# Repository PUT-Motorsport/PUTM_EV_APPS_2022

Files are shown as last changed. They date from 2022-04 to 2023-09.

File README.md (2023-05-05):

# Accelerator Pedal Position Sensor (APPS)

## Motivation

APPS handling is required by official FSG Rules according to T11.8 ([see](https://www.formulastudent.de/fileadmin/user_upload/all/2022/rules/FS-Rules_2022_v1.0.pdf#page=58)). APPS signals are system critical signals meaning that any implausibility between sensors or a failure should result in complete motor power shutdown.

## Pedal travel

* 0% - fully released
* 100% - fully applied

## Implausiblity

Implausibility is defined as a deviation of more than ten percentage points pedal travel
between any of the used APPSs. If it occurs for more than 100 ms the power to the motor must be immediately shut down.

## Platform

Software for APPS signal handling is developed using C++ for STM32 microcontroller.

## Program schematic

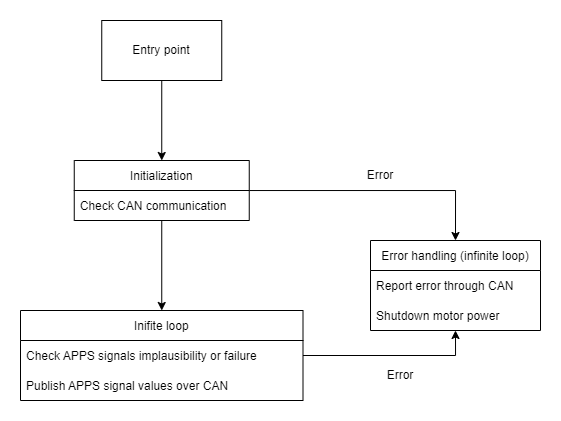
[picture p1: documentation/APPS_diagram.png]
APPS diagram


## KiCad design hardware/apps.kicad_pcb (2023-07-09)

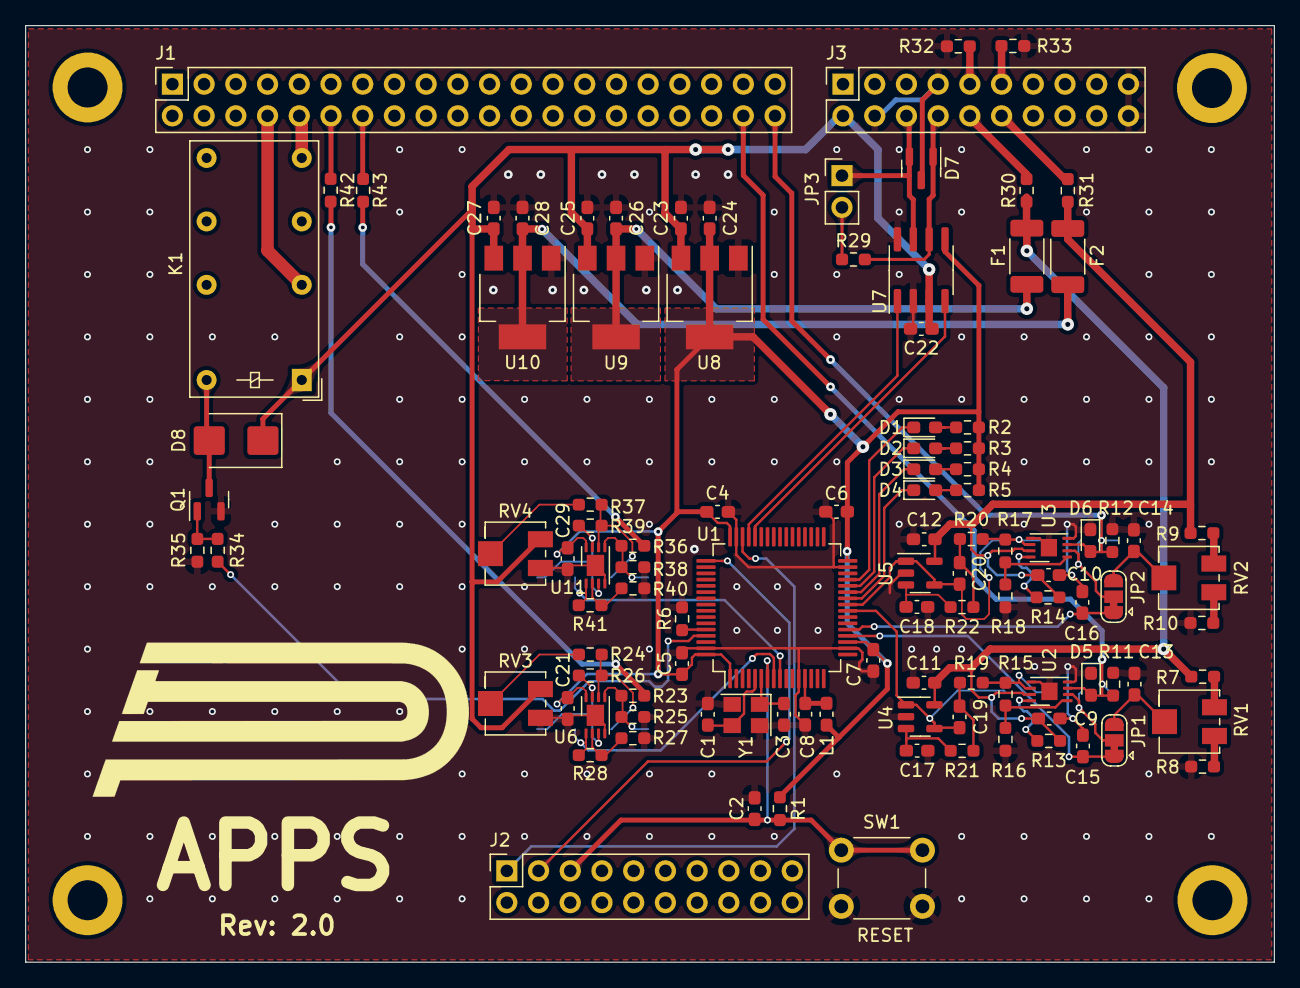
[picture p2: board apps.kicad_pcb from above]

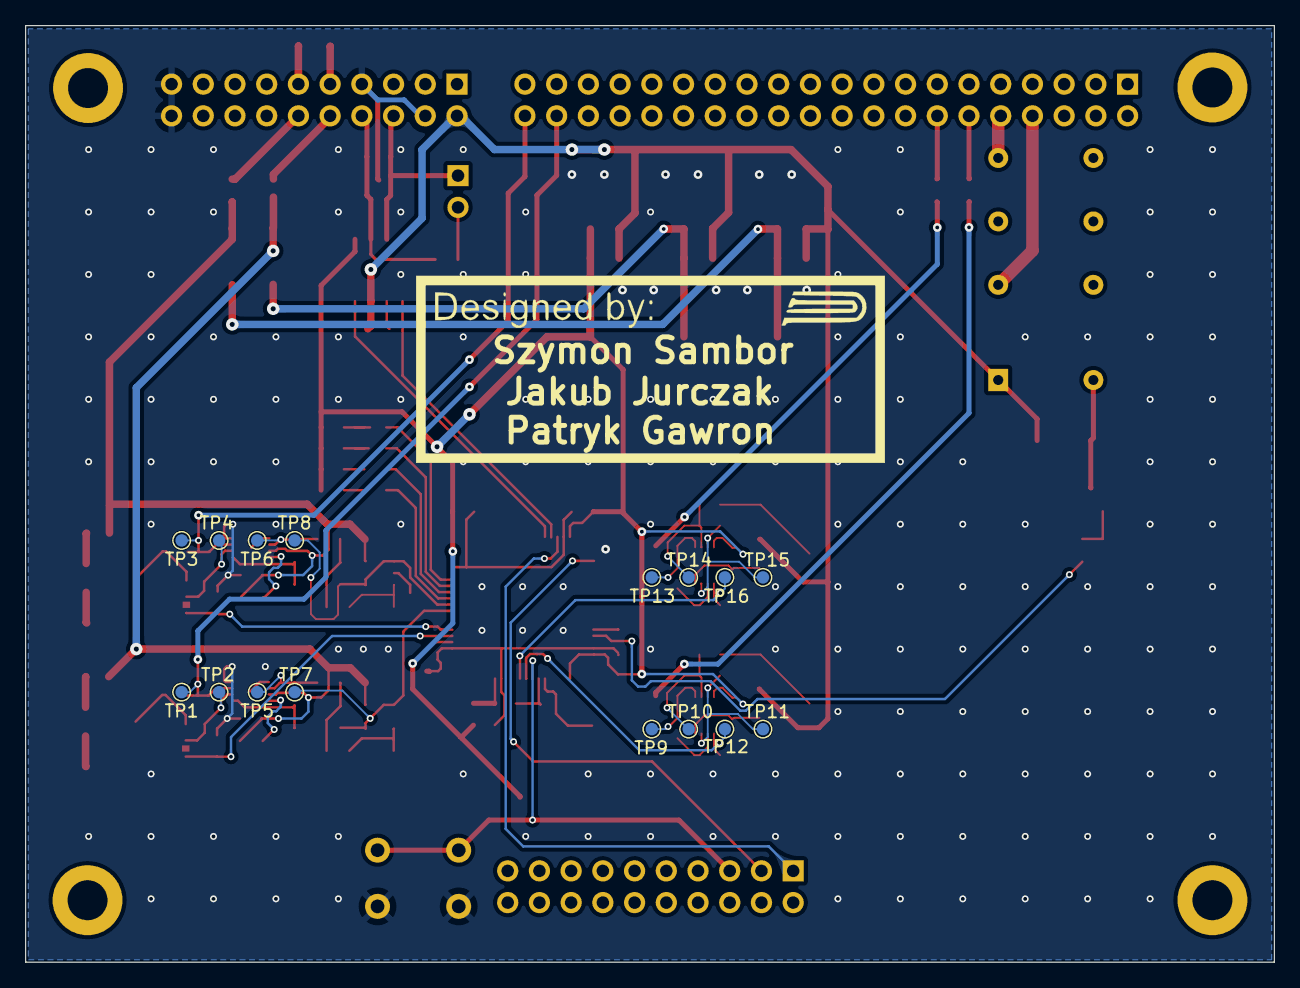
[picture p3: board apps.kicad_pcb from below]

Board: 2 copper layers, 100.0 x 75.0 mm, 124 parts (16 on the bottom side), 76 nets.

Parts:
C1, C3: 22p; C_0603_1608Metric_Pad1.08x0.95mm_HandSolder
C2, C4, C5, C6, C7, C8, C9, C10, C11, C12, C17, C18, C19, C20, C21, C22, C23, C24, C25, C26, C27, C28, C29: 100n; C_0603_1608Metric_Pad1.08x0.95mm_HandSolder
C13, C14, C15, C16: 10n; C_0603_1608Metric_Pad1.08x0.95mm_HandSolder
D1, D2, D3, D4: Yellow; LED_0603_1608Metric_Pad1.05x0.95mm_HandSolder
D5, D6: 24V; D_0603_1608Metric_Pad1.05x0.95mm_HandSolder
D7: PESD2CAN.215; SOT-23
D8: STPS340U; D_SMB
F1, F2: 500mA; Fuse_2010_5025Metric
J1: Signals; PinSocket_2x20_P2.54mm_Vertical
J2: Diagnostics; PinSocket_2x10_P2.54mm_Vertical
J3: Power & CAN; PinSocket_2x10_P2.54mm_Vertical
JP1, JP2: POT/DAC; SolderJumper-3_P1.3mm_Bridged12_RoundedPad1.0x1.5mm
JP3: Terminator; PinHeader_1x02_P2.54mm_Vertical
K1: FINDER-30.22; Relay_DPDT_Finder_30.22
L1: 10u; L_0603_1608Metric_Pad1.05x0.95mm_HandSolder
Q1: BSN20; SOT-23
R1, R6, R7, R9, R35: 10k; R_0603_1608Metric_Pad0.98x0.95mm_HandSolder
R2, R3, R4, R5: 300R; R_0603_1608Metric_Pad0.98x0.95mm_HandSolder
R8, R10: 33k; R_0603_1608Metric_Pad0.98x0.95mm_HandSolder
R11, R12: 100k; R_0603_1608Metric_Pad0.98x0.95mm_HandSolder
R13, R14, R23, R26, R28, R32, R36, R39, R41, R42, R43: 0R; R_0603_1608Metric_Pad0.98x0.95mm_HandSolder
R15, R19, R20, R21, R22: 4k7; R_0603_1608Metric_Pad0.98x0.95mm_HandSolder
R16, R18: 1k; R_0603_1608Metric_Pad0.98x0.95mm_HandSolder
R17: 6k2; R_0603_1608Metric_Pad0.98x0.95mm_HandSolder
R24, R25, R34, R37, R38: 100R; R_0603_1608Metric_Pad0.98x0.95mm_HandSolder
R27, R40: 3k3; R_0603_1608Metric_Pad0.98x0.95mm_HandSolder
R29: 120R; R_0603_1608Metric_Pad0.98x0.95mm_HandSolder
R30: 330R; R_0603_1608Metric_Pad0.98x0.95mm_HandSolder
R31, R33: 220R; R_0603_1608Metric_Pad0.98x0.95mm_HandSolder
RV1, RV2: 1k; Potentiometer_Bourns_3214J_Horizontal
RV3, RV4: 2k; Potentiometer_Bourns_3214J_Horizontal
SW1: Reset; SW_PUSH_6mm
TP1, TP3: APPS_P; TestPoint_Pad_D1.0mm
TP2, TP4: APPS_N; TestPoint_Pad_D1.0mm
TP5, TP6: APPS_MID; TestPoint_Pad_D1.0mm
TP7, TP8: APPS_OUT; TestPoint_Pad_D1.0mm
TP9, TP13: BR_P; TestPoint_Pad_D1.0mm
TP10, TP14: BR_N; TestPoint_Pad_D1.0mm
TP11, TP15: BR_MID; TestPoint_Pad_D1.0mm
TP12, TP16: BR_OUT; TestPoint_Pad_D1.0mm
U1: STM32L4P5RET6; LQFP-64_10x10mm_P0.5mm
U2, U3: MCP6N11-005; TDFN-8-1EP_3x2mm_P0.5mm_EP1.3x1.4mm
U4, U5: MCP6001; SOT-23-5
U6, U11: MCP6002-xMC; DFN-8-1EP_3x2mm_P0.5mm_EP1.7x1.4mm
U7: MCP2562-H-SN; SOIC-8_3.9x4.9mm_P1.27mm
U8, U9, U10: LM1117-3.3; SOT-223-3_TabPin2
Y1: 8MHz; Crystal_SMD_3225-4Pin_3.2x2.5mm

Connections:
3V3_POT1: C9.1, C11.1, F1.1, R7.1, R13.2, R30.1, U2.7 (V+), U4.5 (V+)
3V3_POT2: C10.1, C12.1, F2.1, R9.1, R14.2, R31.1, U3.7 (V+), U5.5 (V+)
+3V3: C4.1, C5.1, C6.1, C7.1, C21.1, C24.1, C29.1, L1.1, R1.2, R2.1, R3.2, R4.2, R5.1, U1.1 (VBAT), U1.19 (VDD), U1.32 (VDD), U1.48 (VDDUSB), U1.64 (VDD), U6.8 (V+), U7.5 (Vio), U8.2 (VO), U11.8 (V+)
+5V: C22.1, C23.1, C25.1, C27.1, D8.1 (K), J3.2, K1.A1, RV3.1, RV4.1, U7.3 (VDD), U8.3 (VI), U9.3 (VI), U10.3 (VI)
/APPS1: C19.2, TP7.1, U1.24 (PC4), U4.1, U4.4 (-)
/APPS2: C20.2, TP8.1, U1.25 (PC5), U5.1, U5.4 (-)
/BRK_PRESS1: R28.1, TP12.1, U1.8 (PC0), U6.1
/BRK_PRESS2: R41.1, TP16.1, U1.9 (PC1), U11.1
/CAN_RX: U1.44 (PA11), U7.4 (RXD)
/CAN_TX: U1.45 (PA12), U7.1 (TXD)
/DAC_REF1: C15.1, JP1.1 (A), U1.20 (PA4)
/DAC_REF2: C16.1, JP2.1 (A), U1.21 (PA5)
/EN_RELAY: R34.2, U1.61 (PB8)
/LED1: D1.1 (K), U1.29 (PB10)
/LED2: D2.1 (K), U1.28 (PB2)
/LED3: D3.1 (K), U1.27 (PB1)
/LED4: D4.1 (K), U1.26 (PB0)
/XTAL1: C1.1, U1.5 (PH0-OSC_IN), Y1.3
/XTAL2: C3.1, U1.6 (PH1-OSC_OUT), Y1.1
BRK_PRESS_LEFT: R23.2, R42.1
BRK_PRESS_RIGHT: R36.2, R43.1
CAN+: D7.2 (A2), J3.6, JP3.1, U7.7 (CANH)
CAN-: D7.1 (A1), J3.8, R29.2, U7.6 (CANL)
CLK: J2.3, U1.49 (PA14)
GND: C1.2, C2.2, C3.2, C4.2, C5.2, C6.2, C7.2, C8.2, C9.2, C10.2, C11.2, C12.2, C13.2, C14.2, C15.2, C16.2, C17.2, C18.2, C21.2, C22.2, C23.2, C24.2, C25.2, C26.2, C27.2, C28.2, C29.2, D5.1 (A1), D6.1 (A1), D7.3 (common), J3.4, J3.7, J3.19, J3.20, Q1.2 (S), R6.1, R8.2, R10.2, R11.2, R12.2, R16.1, R18.1, R25.1, R27.2, R32.1, R33.1, R35.2, R38.1, R40.2, RV3.3, RV4.3, SW1.1, U1.12 (VSSA/VREF-), U1.18 (VSS), U1.31 (VSS), U1.47 (VSS), U1.63 (VSS), U2.4 (V-), U2.5 (RF), U2.9 (EP), U3.4 (V-), U3.5 (RF), U3.9 (EP), U4.2 (V-), U5.2 (V-), U6.4 (V-), U6.9 (V-), U7.2 (VSS), U7.8 (STBY), U8.1 (GND), U9.1 (GND), U10.1 (GND), U11.4 (V-), U11.9 (V-), Y1.2, Y1.4
NRST: C2.1, J2.5, R1.1, SW1.2, U1.7 (NRST)
unnamed: C19.1, R19.2, R21.1
unnamed: C20.1, R20.2, R22.1
unnamed: D1.2 (A), R2.2
unnamed: D2.2 (A), R3.1
unnamed: D3.2 (A), R4.1
unnamed: D4.2 (A), R5.2
unnamed: D8.2 (A), K1.A2, Q1.3 (D)
unnamed: J1.12, R42.2
unnamed: J1.14, R43.2
unnamed: J3.9, R32.2
unnamed: J3.10, R30.2
unnamed: J3.11, R33.2
unnamed: J3.12, R31.2
unnamed: C13.1, JP1.3 (B), RV1.2
unnamed: JP1.2 (C), TP2.1, U2.2 (-)
unnamed: C14.1, JP2.3 (B), RV2.2
unnamed: JP2.2 (C), TP4.1, U3.2 (-)
unnamed: JP3.2, R29.1
unnamed: Q1.1 (G), R34.1, R35.1
unnamed: R7.2, RV1.1
unnamed: R8.1, RV1.3
unnamed: R9.2, RV2.1
unnamed: R10.1, RV2.3
unnamed: R15.2, R19.1, TP5.1, U2.6
unnamed: R17.2, R20.1, TP6.1, U3.6
unnamed: R24.2, RV3.2
unnamed: R37.2, RV4.2
unnamed: R6.2, U1.60 (PH3-BOOT)
unnamed: R13.1, U2.8 (EN)
unnamed: R15.1, R16.2, U2.1 (FG)
unnamed: R14.1, U3.8 (EN)
unnamed: R17.1, R18.2, U3.1 (FG)
unnamed: C17.1, R21.2, U4.3 (+)
unnamed: C18.1, R22.2, U5.3 (+)
unnamed: R26.1, TP11.1, U6.3 (+), U6.7
unnamed: R27.1, R28.2, U6.2 (-)
unnamed: R23.1, R25.2, TP9.1, U6.5 (+)
unnamed: R24.1, R26.2, TP10.1, U6.6 (-)
unnamed: C26.1, F1.2, U9.2 (VO)
unnamed: C28.1, F2.2, U10.2 (VO)
unnamed: R39.1, TP15.1, U11.3 (+), U11.7
unnamed: R40.1, R41.2, U11.2 (-)
unnamed: R36.1, R38.2, TP13.1, U11.5 (+)
unnamed: R37.1, R39.2, TP14.1, U11.6 (-)
SAFETY_IN: J1.8, K1.11
SAFETY_OUT: J1.10, K1.14
SIG_APPS1: D5.2 (A2), J1.38, R11.1, TP1.1, U2.3 (+)
SIG_APPS2: D6.2 (A2), J1.40, R12.1, TP3.1, U3.3 (+)
SWD: J2.1, U1.46 (PA13)
VDDA: C8.1, L1.2, U1.13 (VDDA/VREF+)

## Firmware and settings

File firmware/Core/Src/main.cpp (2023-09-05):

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
/* Includes ------------------------------------------------------------------*/
#include "main.h"

/* USER CODE BEGIN Includes */
#include <stdlib.h>
#include <algorithm>
#include <cstdint>
#include <stdbool.h>
#include <math.h>
#include "Pedal_Map.h"
#include "APPS_Meta.hpp"

#include "PUTM_EV_CAN_LIBRARY/lib/can_interface.hpp"

/* USER CODE END Includes */

/* USER CODE BEGIN PD */
#define huart1 huart4
#define hcan hcan1
/* USER CODE END PD */

ADC_HandleTypeDef hadc1;
ADC_HandleTypeDef hadc2;
DMA_HandleTypeDef hdma_adc1;
DMA_HandleTypeDef hdma_adc2;

CAN_HandleTypeDef hcan1;

DAC_HandleTypeDef hdac1;

TIM_HandleTypeDef htim2;
TIM_HandleTypeDef htim3;
TIM_HandleTypeDef htim4;

UART_HandleTypeDef huart4;

/* USER CODE BEGIN PV */
bool send_CAN_frame;
bool adc_cpl_flag = 0;
using namespace PUTM_CAN;

const std::size_t number_of_apps_sample = 100;
static_assert( number_of_apps_sample%2 == 0,
        "array size must be even because of two sensors" );

uint16_t apps_val_raw[number_of_apps_sample];
uint16_t press_val_raw[number_of_apps_sample];

// FIXME variable to debug
const bool debug_flag = true;
int debug_data[10];
float diff_debug_data;
/* USER CODE END PV */

void SystemClock_Config(void);
void PeriphCommonClock_Config(void);
static void MX_GPIO_Init(void);
static void MX_DMA_Init(void);
static void MX_ADC1_Init(void);
static void MX_CAN1_Init(void);
static void MX_UART4_Init(void);
static void MX_TIM2_Init(void);
static void MX_TIM3_Init(void);
static void MX_DAC1_Init(void);
static void MX_ADC2_Init(void);
static void MX_TIM4_Init(void);
/* USER CODE BEGIN PFP */

void My_CAN_init(void);
std::pair<int, int> get_raw_avg_apps_value();
std::pair<int, int> get_raw_avg_press_value();
bool get_sensors_plausibility(int apps_raw_value_1, int apps_raw_value_2);

/* USER CODE END PFP */

/* USER CODE BEGIN 0 */
void HAL_ADC_ConvCpltCallback(ADC_HandleTypeDef *hadc) {
    adc_cpl_flag = true;
}
/* USER CODE END 0 */

/**
 * @brief  The application entry point.
 * @retval int
 */
int main(void) {
    /* MCU Configuration--------------------------------------------------------*/

    /* Reset of all peripherals, Initializes the Flash interface and the Systick. */
    HAL_Init();

    /* Configure the system clock */
    SystemClock_Config();

    /* Configure the peripherals common clocks */
    PeriphCommonClock_Config();

    /* Initialize all configured peripherals */
    MX_GPIO_Init();
    MX_DMA_Init();
    MX_ADC1_Init();
    MX_CAN1_Init();
    MX_UART4_Init();
    MX_TIM2_Init();
    MX_TIM3_Init();
    MX_DAC1_Init();
    MX_ADC2_Init();
    MX_TIM4_Init();
    /* USER CODE BEGIN 2 */
    // Setup DAC for the offset voltages
    HAL_DAC_Start(&hdac1, DAC_CHANNEL_1);
    HAL_DAC_Start(&hdac1, DAC_CHANNEL_2);
    HAL_DAC_SetValue(&hdac1, DAC_CHANNEL_1, DAC_ALIGN_12B_R, 2583); // ~2200  mV 2733
    HAL_DAC_SetValue(&hdac1, DAC_CHANNEL_2, DAC_ALIGN_12B_R, 2853); // ~2418 mV 3003

    // Turn on safety
    HAL_GPIO_WritePin(SAFETY_GPIO_Port, SAFETY_Pin, GPIO_PIN_SET);

    My_CAN_init();

    // APPS
    HAL_ADC_Start_DMA(&hadc1, reinterpret_cast<uint32_t*>(apps_val_raw), 100);
    HAL_TIM_Base_Start(&htim3);
    HAL_TIM_Base_Start_IT(&htim2);

    // Brake pressure
    HAL_ADC_Start_DMA(&hadc2, reinterpret_cast<uint32_t*>(press_val_raw), 100);
    HAL_TIM_Base_Start(&htim4);

    HAL_GPIO_WritePin(LED_1_GPIO_Port, LED_1_Pin, GPIO_PIN_SET);
    HAL_GPIO_WritePin(LED_2_GPIO_Port, LED_2_Pin, GPIO_PIN_SET);
    HAL_GPIO_WritePin(LED_3_GPIO_Port, LED_3_Pin, GPIO_PIN_SET);

    HAL_Delay(100);
    uint8_t frame_couter = 0;
    bool sensor_plausibility_last = true;

    uint32_t time_change = 0;
    /* USER CODE END 2 */

    /* Infinite loop */
    /* USER CODE BEGIN WHILE */
    while(1) {
        auto bms_hv = PUTM_CAN::can.get_bms_hv_main();
        bool ts_button = PUTM_CAN::can.get_aq_ts_button_new_data();
        bool no_brake = PUTM_CAN::can.get_aq_main().brake_pressure_front < 3600;

        if(PUTM_CAN::can.get_steering_wheel_event_new_data()) {
            HAL_GPIO_WritePin(SAFETY_GPIO_Port, SAFETY_Pin, GPIO_PIN_SET);
            time_change = HAL_GetTick();
        }

        bool wait_after_start = time_change + 1000 > HAL_GetTick();
        if(bms_hv.device_state == PUTM_CAN::BMS_HV_states::AIR_opened and not wait_after_start) {
            HAL_GPIO_WritePin(SAFETY_GPIO_Port, SAFETY_Pin, GPIO_PIN_RESET);
        }

        if(send_CAN_frame) {
            send_CAN_frame = false;
            adc_cpl_flag = false;

            auto [apps_avg_1, apps_avg_2] = get_raw_avg_apps_value();

            if(bool state = get_sensors_plausibility(apps_avg_1, apps_avg_2); !state && !sensor_plausibility_last) {
                // turn led on
                HAL_GPIO_WritePin(LED_1_GPIO_Port, LED_1_Pin, GPIO_PIN_RESET);

                // turn safety off
                //HAL_GPIO_WritePin(SAFETY_GPIO_Port, SAFETY_Pin, GPIO_PIN_SET);

                // send max value to cause fast stop of CT
                int apps_value_to_send = 0;

                while(true) {
                    // frame counter to make sure that all frames are received
                    frame_couter++;
                    frame_couter %= 100;

                    int8_t sensor_diff_to_send { static_cast<int8_t>(std::clamp(diff_debug_data * 100'0.0f, -120.0f, 120.0f)) };

                    // send data
                    // @formatter:off
                    PUTM_CAN::Apps_main apps_data {
                            .pedal_position = static_cast<uint16_t>(apps_value_to_send),
                            .counter = frame_couter,
                            .position_diff = sensor_diff_to_send,
                            .device_state = PUTM_CAN::Apps_states::Sensor_Implausiblity
                    };
                    // @formatter:on

                    auto tx = PUTM_CAN::Can_tx_message(apps_data, PUTM_CAN::can_tx_header_APPS_MAIN);
                    auto tx_status = tx.send(hcan1);
                    if(HAL_StatusTypeDef::HAL_OK != tx_status) {
                        Error_Handler();
                    }
                    HAL_Delay(100);
                }
            } else {
                sensor_plausibility_last = state;
            }

            // range calculation
            int apps_real_1 = (int)std::round(((float)apps_avg_1 - (float)APPS_1_OFFSETTED_MIN) / scale_factor_1);
            int apps_real_2 = (int)std::round(((float)apps_avg_2 - (float)APPS_2_OFFSETTED_MIN) / scale_factor_2);

            // clamping real values
            int apps_temp_1 = std::clamp(apps_real_1, APPS_REAL_MIN, APPS_REAL_MAX);
            int apps_temp_2 = std::clamp(apps_real_2, APPS_REAL_MIN, APPS_REAL_MAX);

            // get average value of two sensors
            int apps_temp = (apps_temp_1 + apps_temp_2) / 2;

            // non linear curve
            int apps_value_to_send = apps_nonlinear_curve(apps_temp, APPS_map_profile::APPS_MAP_1_linear);

            // frame counter to make sure that all frames are received
            frame_couter++;
            frame_couter %= 100;

            int8_t sensor_diff_to_send { static_cast<int8_t>(std::clamp(diff_debug_data * 100'0.0f, -120.0f, 120.0f)) };

            // send data
            // @formatter:off
            PUTM_CAN::Apps_main apps_data {
                .pedal_position = static_cast<uint16_t>(apps_value_to_send),
                .counter = frame_couter, .position_diff = sensor_diff_to_send,
                .device_state = PUTM_CAN::Apps_states::Normal_operation
            };
            // @formatter:on

            auto tx = PUTM_CAN::Can_tx_message(apps_data, PUTM_CAN::can_tx_header_APPS_MAIN);
            auto tx_status = tx.send(hcan1);
            if(HAL_StatusTypeDef::HAL_OK != tx_status) {
                Error_Handler();
            }

            // Input: 0-3000 Psi (200 Bar)
            // Output: 0.5-4.5 V
            // Formula: pressure (Bars) = 50 * voltage (V) - 25
            auto [press_avg_1, press_avg_2] = get_raw_avg_press_value();
            float pressure_voltage = 3.3 * press_avg_1 / 4096;
            float pressure_voltage2 = 3.3 * press_avg_2 / 4096;
            // @formatter:off
            PUTM_CAN::AQ_main aq {
                .brake_pressure_front = static_cast<uint16_t>((50 * pressure_voltage - 25) * 10),
                .brake_pressure_back = static_cast<uint16_t>((50 * pressure_voltage2 - 25) * 10),
            };
            // @formatter:on
            auto tx_aq = PUTM_CAN::Can_tx_message(aq, PUTM_CAN::can_tx_header_AQ_MAIN);
            if(HAL_StatusTypeDef::HAL_OK not_eq tx_aq.send(hcan1)) {
                Error_Handler();
            }

            // FIXME debug data
            if constexpr (debug_flag) {
                debug_data[0] = apps_avg_1;
                debug_data[1] = apps_avg_2;

                debug_data[2] = apps_real_1;
                debug_data[3] = apps_real_2;

                debug_data[4] = apps_temp_1;
                debug_data[5] = apps_temp_2;

                debug_data[6] = apps_temp;

                debug_data[7] = apps_value_to_send;
            }
        }
        /* USER CODE END WHILE */

        /* USER CODE BEGIN 3 */
    }
    /* USER CODE END 3 */
}

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
/* USER CODE BEGIN 4 */
void My_CAN_init(void) {
constexpr static CAN_FilterTypeDef sFilterConfig {
    .FilterIdHigh = 0x0000,
    .FilterIdLow = 0x0000,
    .FilterMaskIdHigh = 0x0000,
    .FilterMaskIdLow = 0x0000,
    .FilterFIFOAssignment = CAN_RX_FIFO0,
    .FilterBank = 0,
    .FilterMode = CAN_FILTERMODE_IDMASK,
    .FilterScale = CAN_FILTERSCALE_32BIT,
    .FilterActivation = ENABLE,
    .SlaveStartFilterBank = 14
}
;

if (HAL_CAN_ConfigFilter(&hcan, &sFilterConfig) != HAL_OK) {
    Error_Handler();
}

if (HAL_CAN_Start(&hcan) != HAL_OK) {
    Error_Handler();
}

if (HAL_CAN_ActivateNotification(&hcan, CAN_IT_RX_FIFO0_MSG_PENDING | CAN_IT_TX_MAILBOX_EMPTY) != HAL_OK) {
    Error_Handler();
}
}

std::pair<int, int> get_raw_avg_apps_value() {
float apps_temp_raw_sum_1 = 0;
float apps_temp_raw_sum_2 = 0;

for(unsigned int i = 0; i < number_of_apps_sample; i = i + 2) {
    apps_temp_raw_sum_1 += apps_val_raw[i];
    apps_temp_raw_sum_2 += apps_val_raw[i + 1];
}

int apps_temp_raw_avg_1 = (int)(apps_temp_raw_sum_1 / ((float)number_of_apps_sample / 2.0f));
int apps_temp_raw_avg_2 = (int)(apps_temp_raw_sum_2 / ((float)number_of_apps_sample / 2.0f));

return std::make_pair(apps_temp_raw_avg_1, apps_temp_raw_avg_2);
}

std::pair<int, int> get_raw_avg_press_value() {
float press_temp_raw_sum_1 = 0;
float press_temp_raw_sum_2 = 0;

for(unsigned int i = 0; i < number_of_apps_sample; i = i + 2) {
    press_temp_raw_sum_1 += press_val_raw[i];
    press_temp_raw_sum_2 += press_val_raw[i + 1];
}

int press_temp_raw_avg_1 = (int)(press_temp_raw_sum_1 / ((float)number_of_apps_sample / 2.0f));
int press_temp_raw_avg_2 = (int)(press_temp_raw_sum_2 / ((float)number_of_apps_sample / 2.0f));

return std::make_pair(press_temp_raw_avg_1, press_temp_raw_avg_2);
}

bool get_sensors_plausibility(int apps_raw_value_1, int apps_raw_value_2) {

/* T 11.8.9 Implausibility is defined as a deviation of more than ten percentage points pedal travel
 between any of the used APPSs or any failure according to T 11.9.
 */

// fraction of full scale position
float apps_scaled_1 = ((float)apps_raw_value_1 - (float)APPS_1_OFFSETTED_MIN) / (float)APPS_1_RAW_FULLSCALE;
float apps_scaled_2 = ((float)apps_raw_value_2 - (float)APPS_2_OFFSETTED_MIN) / (float)APPS_2_RAW_FULLSCALE;

float diff = fabsf(apps_scaled_1 - apps_scaled_2);

debug_data[9] = static_cast<int>(diff * 100);
diff_debug_data = diff;

if(diff > sensor_implausibility_factor) {
    return false;
} else {
    return true;
}

}

/* USER CODE END 4 */
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


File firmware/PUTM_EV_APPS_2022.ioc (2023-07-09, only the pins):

Mcu.UserName=STM32L4P5RETx
PA0.Signal=UART4_TX
PA1.Signal=UART4_RX
PA11.GPIO_Label=CAN_RX
PA11.Signal=CAN1_RX
PA12.GPIO_Label=CAN_TX
PA12.Signal=CAN1_TX
PA4.GPIO_Label=DAC_REF1
PA4.Signal=COMP_DAC11_group
PA5.GPIO_Label=DAC_REF2
PA5.Signal=COMP_DAC12_group
PB0.GPIO_Label=LED_4
PB0.Signal=GPIO_Output
PB1.GPIO_Label=LED_3
PB1.Signal=GPIO_Output
PB10.GPIO_Label=LED_1
PB10.Signal=GPIO_Output
PB2.GPIO_Label=LED_2
PB2.Signal=GPIO_Output
PB8.GPIO_Label=SAFETY
PB8.Signal=GPIO_Output
PC0.GPIO_Label=BRK_PRESS1
PC0.Signal=ADCx_IN1
PC1.GPIO_Label=BRK_PRESS2
PC1.Signal=ADCx_IN2
PC4.GPIO_Label=SENSOR_1
PC4.Signal=ADCx_IN13
PC5.GPIO_Label=SENSOR_2
PC5.Signal=ADCx_IN14

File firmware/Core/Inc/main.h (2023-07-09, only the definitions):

#define BRK_PRESS1_Pin GPIO_PIN_0
#define BRK_PRESS1_GPIO_Port GPIOC
#define BRK_PRESS2_Pin GPIO_PIN_1
#define BRK_PRESS2_GPIO_Port GPIOC
#define DAC_REF1_Pin GPIO_PIN_4
#define DAC_REF1_GPIO_Port GPIOA
#define DAC_REF2_Pin GPIO_PIN_5
#define DAC_REF2_GPIO_Port GPIOA
#define SENSOR_1_Pin GPIO_PIN_4
#define SENSOR_1_GPIO_Port GPIOC
#define SENSOR_2_Pin GPIO_PIN_5
#define SENSOR_2_GPIO_Port GPIOC
#define LED_4_Pin GPIO_PIN_0
#define LED_4_GPIO_Port GPIOB
#define LED_3_Pin GPIO_PIN_1
#define LED_3_GPIO_Port GPIOB
#define LED_2_Pin GPIO_PIN_2
#define LED_2_GPIO_Port GPIOB
#define LED_1_Pin GPIO_PIN_10
#define LED_1_GPIO_Port GPIOB
#define CAN_RX_Pin GPIO_PIN_11
#define CAN_RX_GPIO_Port GPIOA
#define CAN_TX_Pin GPIO_PIN_12
#define CAN_TX_GPIO_Port GPIOA
#define SAFETY_Pin GPIO_PIN_8
#define SAFETY_GPIO_Port GPIOB

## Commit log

2022-04-27 .gitignore for Kicad and STM32 project
2022-04-27 STM32 project config + hardware files clean up
    [APPS.kicad_pcb, APPS.kicad_sch, APPS.sch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]
2022-05-27 Tests on table config
    [PUTM_EV_APPS_2022 Debug.cfg]
2022-05-27 Working CAN interface and calibrated for pedal table stand.
2022-05-28 Corrected .gitignore to include Startup folder in Core
    [main.cpp]
2022-05-29 Tested with TCS on cable harness + calibrated for car pedal.
2022-06-05 Calibration for PM-08
2022-06-22 New CAN lib + core refactor
    [FIRMWARE\PUTM_EV_APPS_2022 Debug.cfg]
2022-07-24 Calibration 24.07.2022 new pedal mount.
2022-09-06 TS activation button + apps calibration
2023-04-11 Use in-amps for the analog inputs
    [APPS.kicad_sch, AnalogInputs.kicad_sch, CAN.kicad_sch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]
2023-04-21 Align components on the PCB
    [APPS.kicad_pcb, APPS.kicad_sch, AnalogInputs.kicad_sch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]
2023-04-21 KiCad project refactor
    [APPS.kicad_pcb, APPS.kicad_sch, CAN.kicad_sch]
2023-04-22 Route PCB tracks
    [APPS.kicad_pcb, APPS.kicad_sch, AnalogInputs.kicad_sch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]
2023-04-22 Rename directories
    [APPS.kicad_pcb, APPS.kicad_sch, APPS.sch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]
2023-05-02 Add brake pressure sensors
    [APPS.kicad_pcb, APPS.kicad_sch, AnalogInputs.kicad_sch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]
2023-05-02 Add 0R resistors to the brake pressure signals
    [APPS.kicad_pcb, APPS.kicad_sch, Connectros.kicad_sch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]
2023-05-02 Use bridged solder jumpers
    [APPS.kicad_pcb, AnalogInputs.kicad_sch]
2023-05-02 Change test points footprints
    [APPS.kicad_pcb, AnalogInputs.kicad_sch, brake_pressure.kicad_sch]
2023-06-23 Update component values
    [analog_inputs.kicad_sch, apps.kicad_pcb, apps.kicad_sch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]
2023-06-30 Adjust APPS values and implement brake pressure measurements
2023-06-30 Adjust component values
    [analog_inputs.kicad_sch, apps.kicad_pcb, apps.kicad_sch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]
2023-07-08 Use voltage followers for the brake pressure measurements
    [apps.kicad_pcb, brake_pressure.kicad_sch]
2023-07-08 Send the real brake pressure values
2023-07-14 Don't send data from the second sensors for now
2023-08-20 Send data from the second brake pressure sensor

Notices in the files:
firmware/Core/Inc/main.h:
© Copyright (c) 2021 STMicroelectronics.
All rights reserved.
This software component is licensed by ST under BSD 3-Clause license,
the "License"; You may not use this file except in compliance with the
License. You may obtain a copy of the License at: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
